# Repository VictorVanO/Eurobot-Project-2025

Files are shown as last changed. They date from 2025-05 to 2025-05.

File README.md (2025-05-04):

# Eurobot-Project-2025




# Table of contents

* [Project participants](#project-participants)
* [About the project](#question-about-the-project)
* [Getting started](#rocket-getting-started)
    * [Prerequesites](#exclamation-prerequesites)
* [Big Robot](#car-big-robot)
* [PAMI](#pami)
    * [Superstar](#star2-superstar)
    * [Groupie](#dancer-groupie)
* [Tree structure](#deciduous_tree-tree-structure)

# Project participants
- 20253 Van Olffen Victor
- 195030 Jardinet Louis
- 18194 Dufour Arthur
- 195105 Simpalingabo Ange
- 195357 Comor Edin
- 195052 Sahib Oussama

# :question: About the project
The purpose of this project is to participate in the [Eurobot Contest][eurobot] organised in 2025. The rules are available [here][eurobot-rules].

Our participation to this competition was necessary in order to validate the **Embedded Project** course given in 1st year of informatics/electronics at ECAM.

# :rocket: Getting started

This repository is a presentation of our robots and our strategies.

Anyone willing to replicate our robots should be able to do so using this repository.

Every file we used for our robots are listed here, aswell as the components and the schematics.

 Below is a photo of our robots (1 Big robot and 2 PAMI units):
 <p align="center">
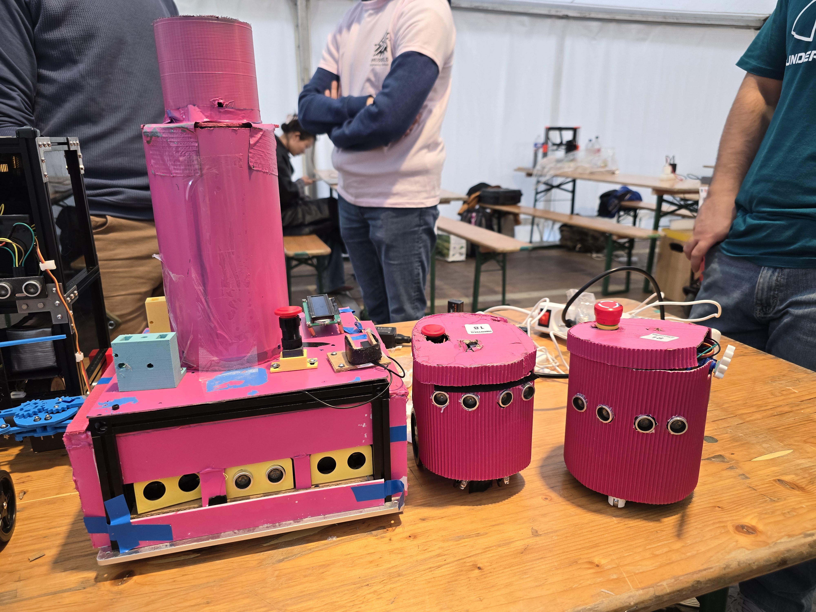
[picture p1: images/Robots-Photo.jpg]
Photo Robots
    
 </p>

## :exclamation: Prerequesites

To use our codes, you will need:
- [Arduino IDE][arduino] - To compile, debug and upload the .ino files into the arduino hardwares

You will also need to install these arduino libraries:
- LiquidCrystal_I2C
- Servo

# :car: Big Robot

## 🧩 Bloc Diagram
The Bloc diagram below shows the main components of the Big robot and how they are connected together.
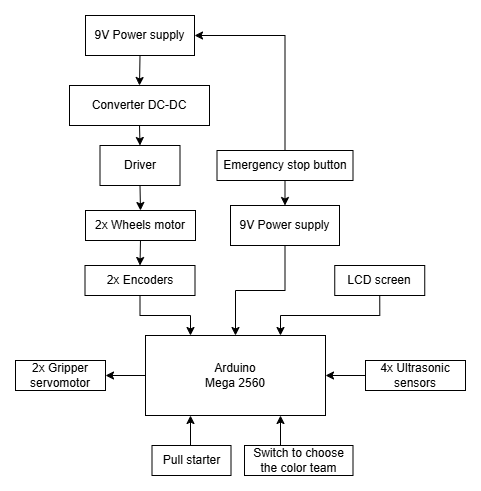
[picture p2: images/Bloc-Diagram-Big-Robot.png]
Bloc Diagram of the big robot.


## :memo: FSM

Our [initial FSM][fsm-big-robot-init] was ambitious, but due to a lack of time and components, our final FSM ended up like this:

Finite-State Machine of the big robot.

## :wrench: Components
Here are the main components for our robot : 
- 2 x 9V rechargeable power supplies to separately supply the driver and the microcontroller
- 2 x Voltage regulators
- 1 x Cytron MDD10A Dual Motors Driver
- 1 x Arduino Mega 2560
- 8 x HC-SR04 Ultrasonic sensors
- 2 x 3D Printed Robotic Arms
- 1 x Aluminium 25x25 cm frale
- 2 x DC Motors with corresponding wheels
- 1 x breadboard
- 1 x Emergency Button
- 1 x Starting Magnetic Reed
   
## Strategy
The Big Robot is designed to perform a specific sequence of actions to score points during the match:

1. **Banner Deployment :**  
   The robot starts by deploying the banner. The first gripper releases its tube, allowing the first banner holder to drop and clip into the edge of the table. Then, the robot moves forward by about 20 cm, and the second gripper releases the second tube, completing the deployment of the banner.

2. **Repositioning :**  
   After the banner is fully deployed, the robot reverses and begins its path toward the arrival zone, stopping right in front of it.

3. **Timed Entry :**  
   The robot waits until approximately the 85th second, allowing the 2 PAMI robots to clear the area.

4. **Final Movement :**  
   As soon as the area is clear, the Big Robot enters the arrival zone to secure end-of-match points.

## Schematic wiring

This is the schematic circuit of the big robot :
 
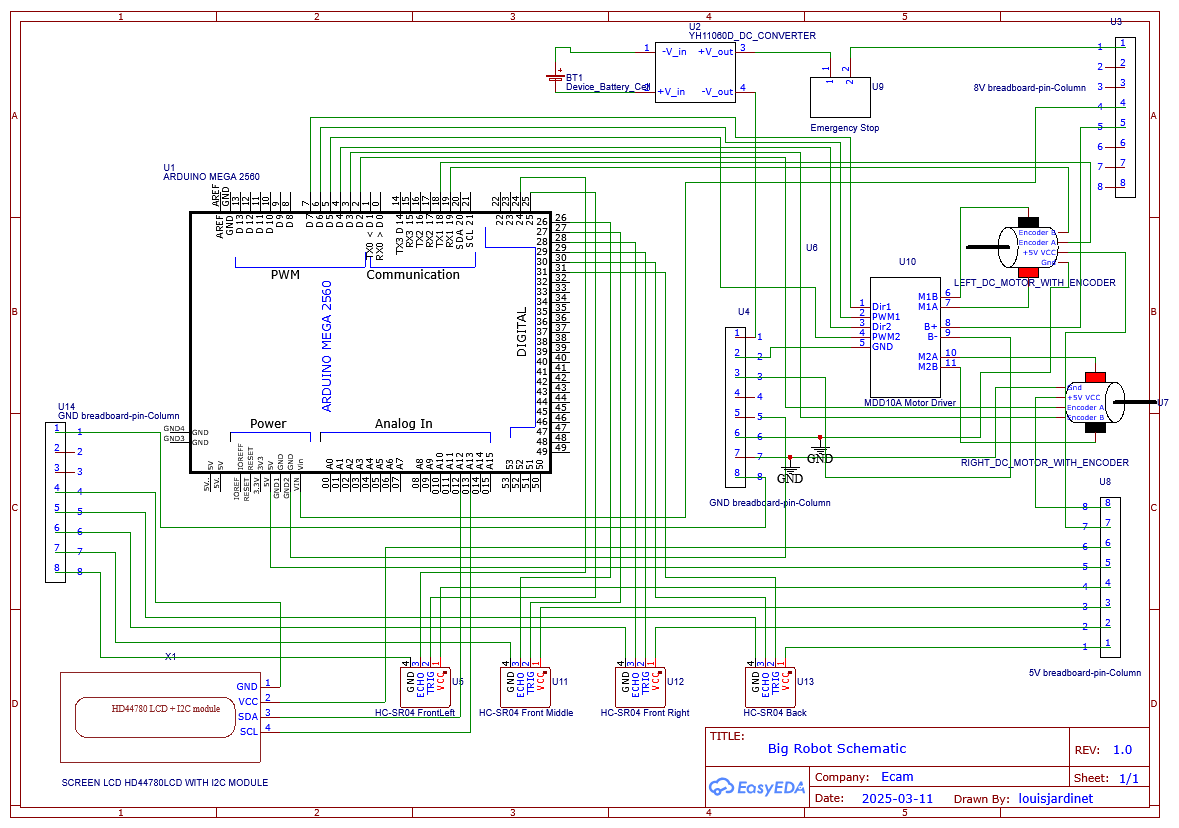
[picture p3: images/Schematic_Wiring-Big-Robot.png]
Schematic wiring of the big robot


## Grippers
The Big Robot is now equipped with 2 independent grippers, each controlled by a servo motor and mounted on a dedicated gripper support.
Each gripper holds one end of a tube, and each tube is attached to a banner holder shaped to fit the edge of the match table.
The banner itself measures 60 cm in length and 25 cm in height.

<p align="center">
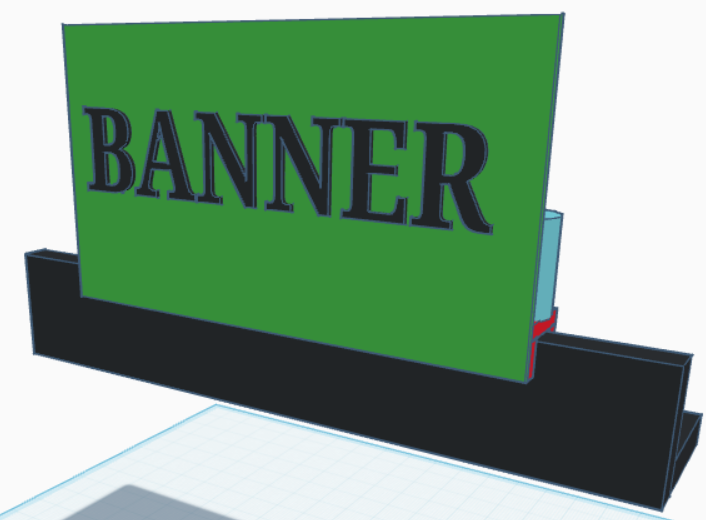
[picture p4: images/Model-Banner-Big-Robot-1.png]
Model Banner Step 1
  
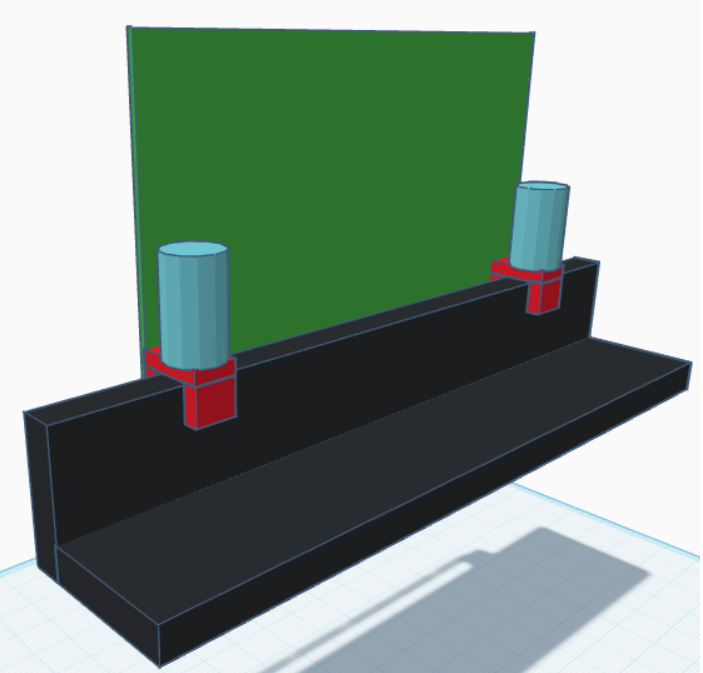
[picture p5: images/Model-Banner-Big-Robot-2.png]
Model Banner Step 2
  
</p>

During deployment, the robot releases the 1st tube, allowing the 1st banner holder to drop and clip into the table edge.
Then, the robot moves forward about 20 cm and releases the 2nd tube, completing the deployment of the banner.

In the ```3D-Models/big-robot``` folder, you’ll find the STL file for the gripper support. This part needs to be printed twice — once for each gripper:

| STL File | Required Quantity |
|---|---|
| gripper-support.stl | 2 |

# PAMI

## Components
 Here are the main components for ours PAMI's : 
 - 1 x Arduino Adafruits
 - 2 x HC-SR04 Ultrasonic sensors
 - 2 x Infrared sensors
 - 2 x DC Motors with corresponding wheels
 - 1 x breadboard
 - 1 x Emergency Button
 - 2 x Optical encoders
 - 1 x Servomotor
 - 1 x LED

# :star2: Superstar

## 🧩 Bloc Diagram
The Bloc diagram below shows the main components of the Superstar and how they are connected together :
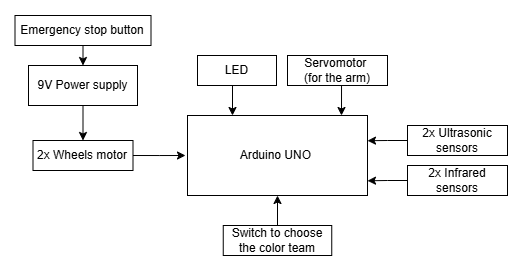
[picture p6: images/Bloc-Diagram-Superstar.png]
Bloc Diagram of the big robot.


## :memo: FSM

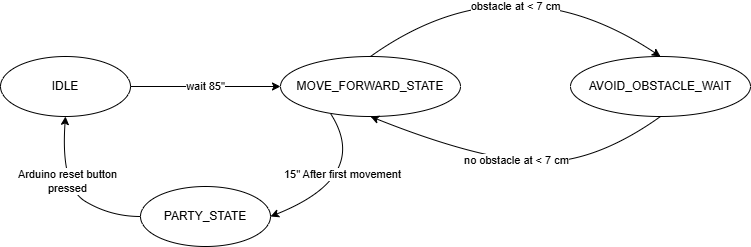
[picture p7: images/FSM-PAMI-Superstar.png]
Finite-State Machine of the PAMI superstar.


## Sensors

- **Distance Sensor (Ultrasonic)**  
    Detects obstacles from a distance to enable automatic avoidance and spatial orientation.

## Strategy
In order to score points the Superstar should be able to : 
1. The robot climbs the ramp by moving straight for 6 seconds at full speed.
2. It then turns right for 1.5 seconds to align itself as close as possible to the edge of the platform to maximize scoring potential.
3. It drives forward briefly to stabilize or adjust its final position.
4. Enter PARTY_STATE to celebrate the arrival. In this state, the robot rotates its servo motor arms back and forth and blinks the LED lights to provide a visual and animated signal.
   
## Obstacle Avoidance
When an obstacle is detected by the distance sensor, the robot stop until there is no more obstacle. 

## Schematic wiring

This is the schematic circuit of the superstar :

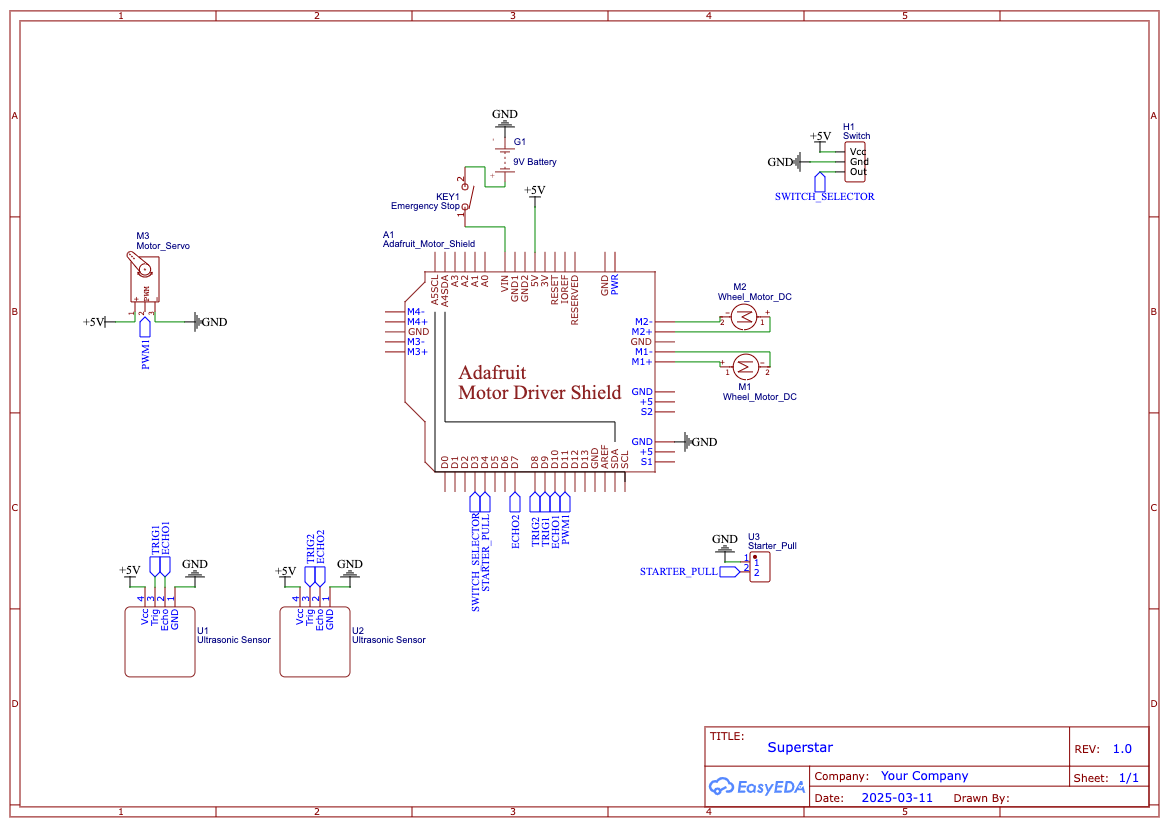
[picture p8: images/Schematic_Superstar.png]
Schematic wiring of the Superstar robot


### Obstacle Avoidance
When an obstacle is detected by the distance sensor, the robot stop until there is no more obstacle. 

## Assembly 
- The two motors and encoders are already placed on the chassis
- Glue the breadboard to the chassis
- With four M3x20mm screws, attach the Arduino mount on the second plate and place the Arduino in it
- With four M3x15mm standoff screws, assemble the two plates
- With two M3x30mm screws fix the Ultrasonic sensor mount on the front of the Arduino mount and slide the sensors into the support
- With two M3x20mm standoff screws fix the Servo/Emergency button mount on the rear of the Arduino mount and slide motor and the button into the support
- With two M3 screws and nuts fix the battery support to the lower plate

# :dancer: Groupie

## 🧩 Bloc Diagram
The Bloc diagram below shows the main components of the Groupie and how they are connected together :
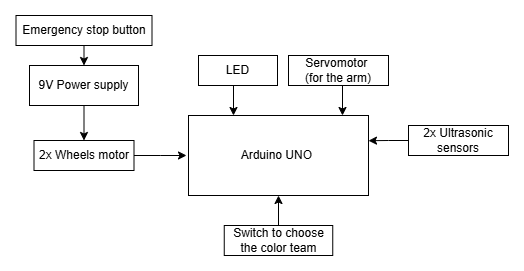
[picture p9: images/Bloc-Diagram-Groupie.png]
Bloc Diagram of the big robot.


## :memo: FSM

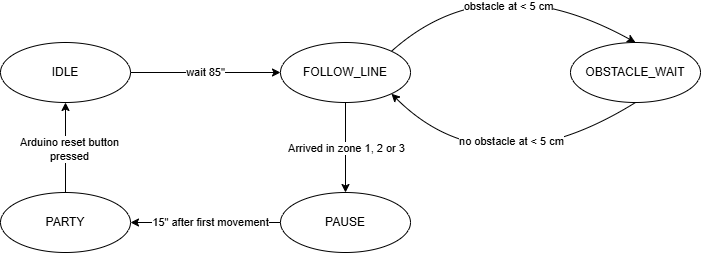
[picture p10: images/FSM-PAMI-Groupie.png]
Finite-State Machine of the PAMI groupie.


## Sensors

- **Infrared (IR) Sensors**  
    Used for line-following and distinguishing between black and white surfaces. Placed at the front of the robot, they allow it to follow a line on the ground or detect nearby obstacles.

- **Optical Fork Sensors (Encoders)**  
    Each wheel is equipped with a slotted disk attached to the motor shaft and an optical fork sensor that detects interruptions of the infrared beam caused by the slots. For every detected interruption, a pulse is generated on a microcontroller's digital input. This allows the robot to repeat the same movements on both wheels, improving synchronization and control.

- **Distance Sensor (Ultrasonic)**  
    Detects obstacles from a distance to enable automatic avoidance and spatial orientation.

## Strategy
In order to score points the groupie should be able to : 
1. Follow a line to reach the arrival zone. The robot follows a black line on a light surface using IR sensors. By analyzing the left/right sensor signals, it adjusts its trajectory to stay centered on the line.
2. Enter PARTY_STATE to celebrate the arrival. In this state, the robot rotates its servo motor arms back and forth and blinks the LED lights to provide a visual and animated signal.

## Schematic wiring

This is the schematic circuit of the groupie :

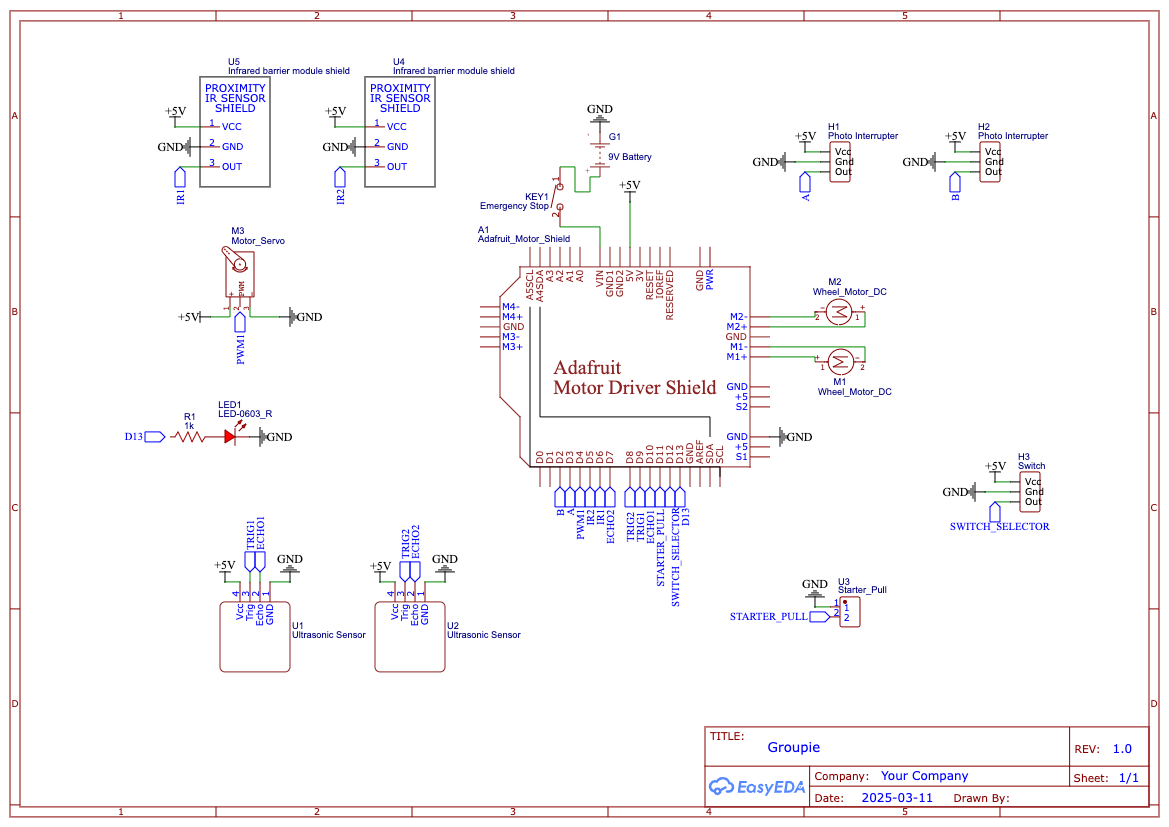
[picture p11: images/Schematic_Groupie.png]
Schematic wiring of the Groupie robot


## Obstacle Avoidance

When an obstacle is detected by the distance sensor, the robot interrupts line following and performs an avoidance maneuver based on a simple algorithm (stop, turn, go forwoard, turn).

## Assembly 
- Place the two motors on the first robot plate and assure that it is positioned on the appropriate holes. Mount the encoder wheels on the inside of the motors
- On the second plate, place the encoders on there dedicated mount 
- With two M3x15mm screws and nuts, fix the Infrared sensors mount at the front of the second plate and fix the sensors on the mount with two M3x15mm screws and nuts
- With four M3x20mm screws, attach the Arduino mount on the second plate and place the Arduino in it
- With four M3x15mm standoff screws, assemble the two red plates. Be sure to keep the motors well in place as they will fixed between the two plates and guide the encoder wheels trough the sensors
- With two M3x30mm screws fix the Ultrasonic sensor mount on the front of the Arduino mount and slide the sensors into the support
- With two M3x20mm standoff screws fix the Servo/Emergency button mount on the rear of the Arduino mount and slide motor and the button into the support

# :deciduous_tree: Tree Structure

```bash
Eurobot-Project-2025
    ├── 3D-models
       ├── big-robot
       ├── groupie-robot
       └── superstar-robot
    ├── big-robot
    ├── groupie-robot
    ├── images
    ├── superstar-robot
    ├── .gitignore
    ├── LICENSE
    └── README.md
```

<!-- Links -->
[eurobot]: https://www.eurobot.org/
[eurobot-rules]: https://www.eurobot.org/eurobot-contest/eurobot-2025/
[arduino]: https://www.arduino.cc/en/software/
[fsm-big-robot-init]: https://github.com/VictorVanO/Eurobot-Project-2025/blob/main/images/FSM-Big-Robot-init.png

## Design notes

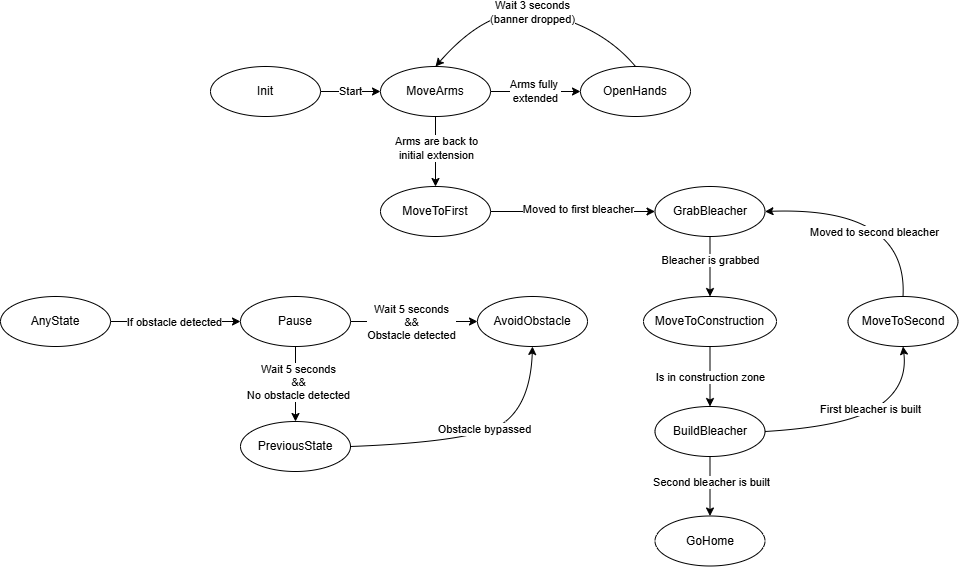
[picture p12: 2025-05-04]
images/FSM-Big-Robot-init.png

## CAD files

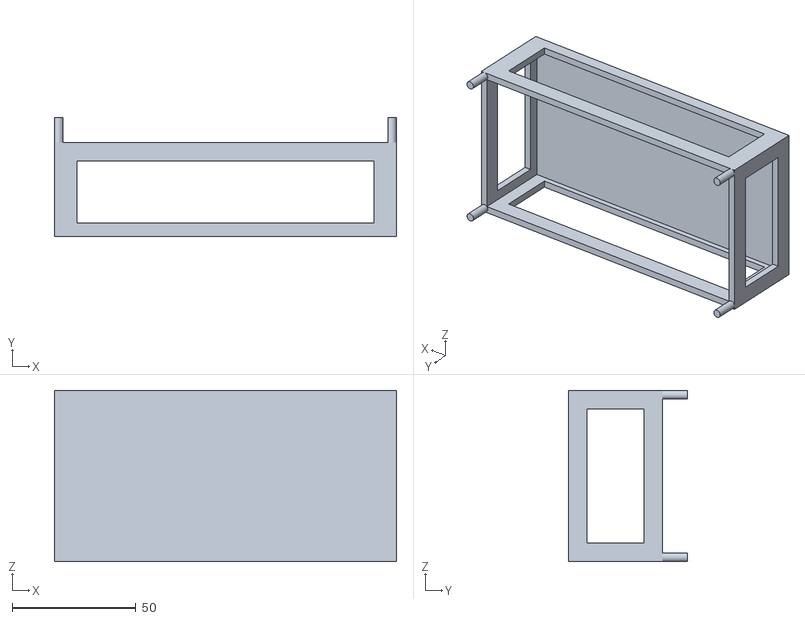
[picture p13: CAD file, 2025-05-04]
3D-models/big-robot/battery-regulator-support.stl
138.0 x 48.0 x 69.0

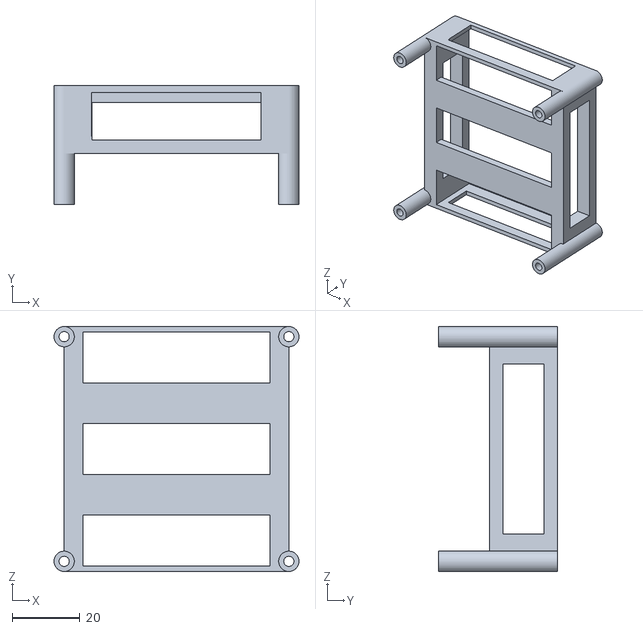
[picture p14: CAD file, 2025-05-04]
3D-models/groupie-robot/arduino-uno-support.stl
72.2 x 35.0 x 72.2

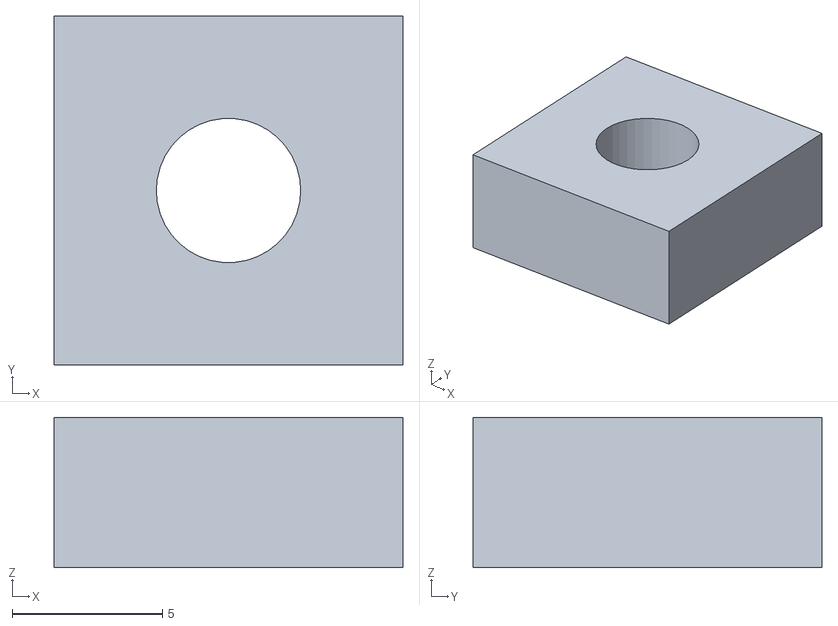
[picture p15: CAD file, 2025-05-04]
3D-models/groupie-robot/arm/arm-fix.stl
11.6 x 11.6 x 5.00

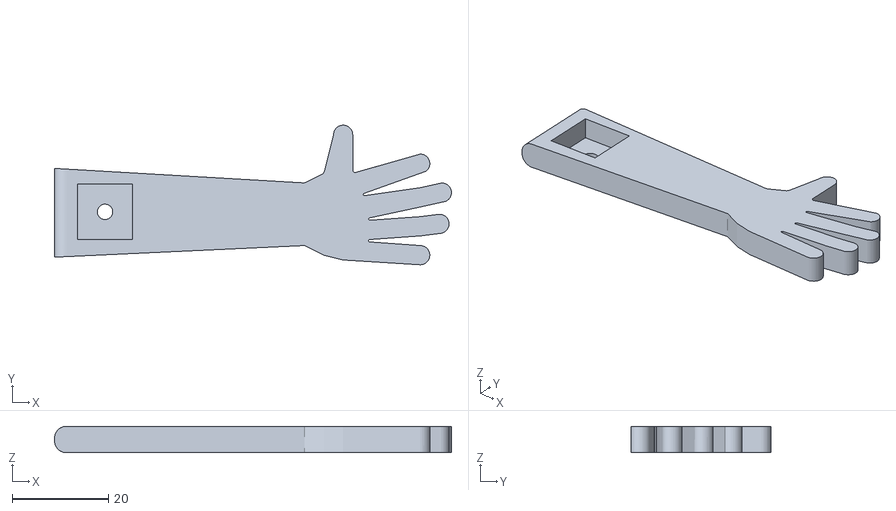
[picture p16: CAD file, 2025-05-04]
3D-models/superstar-robot/arm/arm.stl
82.4 x 29.0 x 5.50

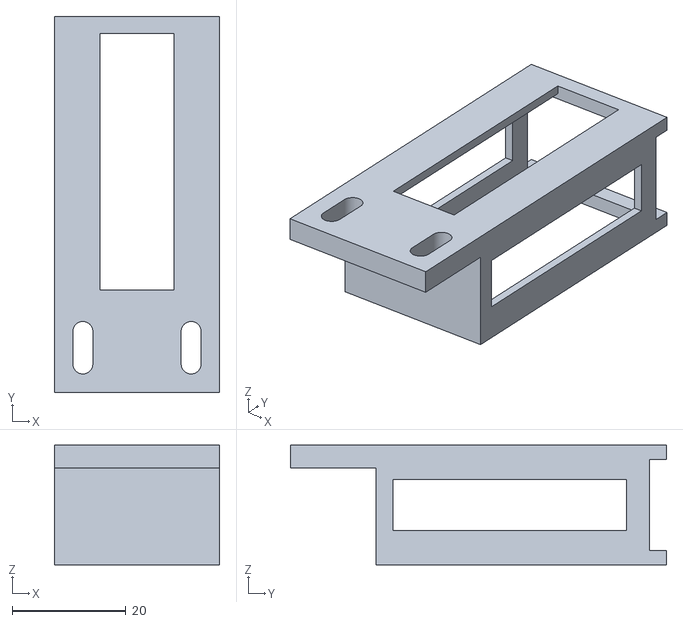
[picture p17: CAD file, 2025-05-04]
3D-models/superstar-robot/battery-support.stl
29.0 x 66.0 x 21.0

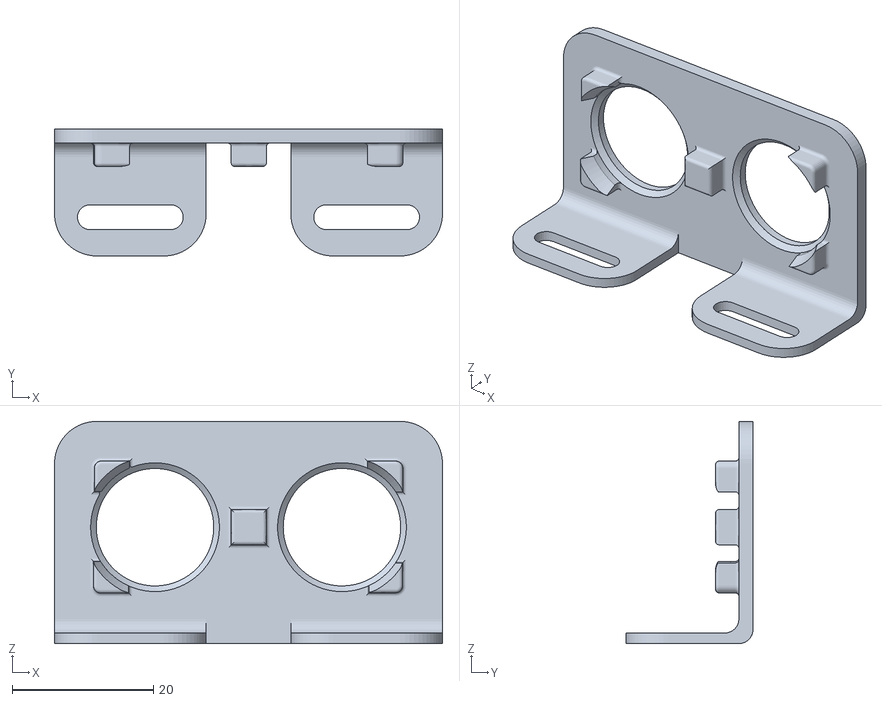
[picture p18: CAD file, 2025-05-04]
3D-models/big-robot/ultrasonic-sensor-support.stl
55.0 x 18.0 x 31.5

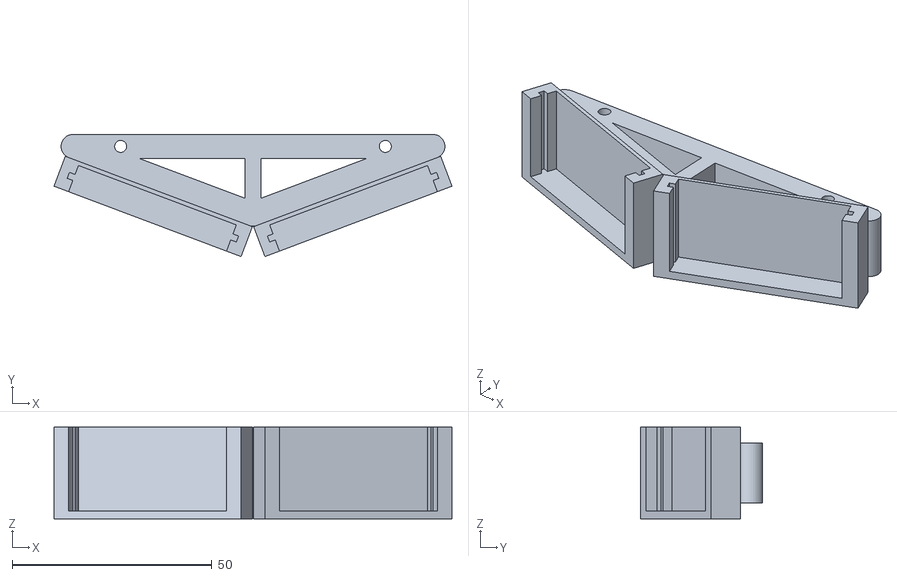
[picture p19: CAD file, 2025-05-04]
3D-models/groupie-robot/double-ultrasonic-sensor-support.stl
99.5 x 30.6 x 23.0

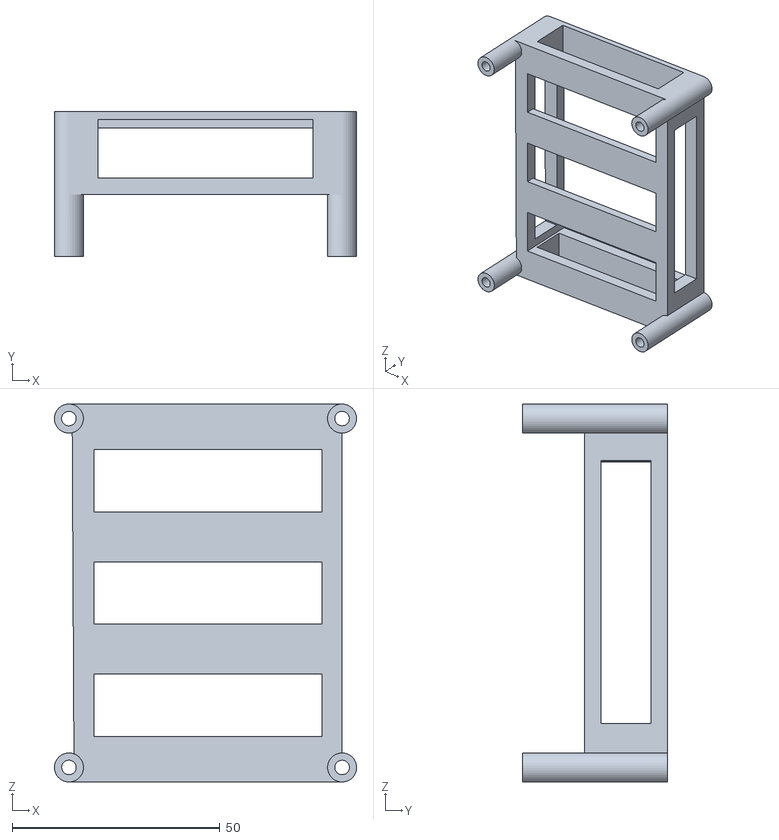
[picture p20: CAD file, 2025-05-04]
3D-models/superstar-robot/arduino-uno-support.stl
72.8 x 35.0 x 91.0

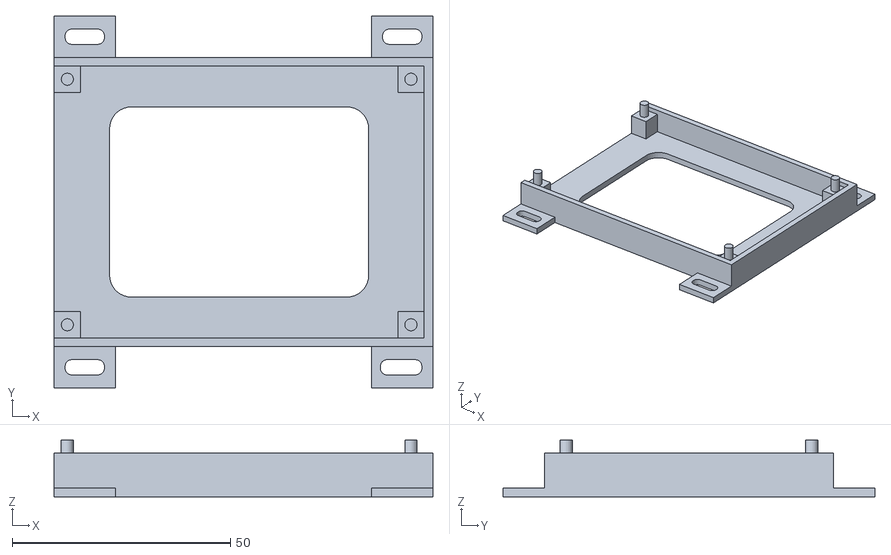
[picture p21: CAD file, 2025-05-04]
3D-models/big-robot/driver-motor-dc-support.stl
86.8 x 85.3 x 13.0

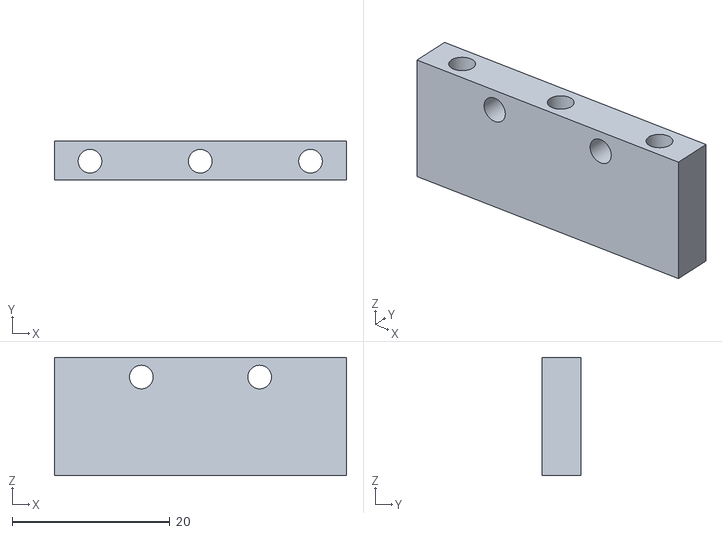
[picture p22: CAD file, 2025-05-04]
3D-models/groupie-robot/double-infrared-sensor-support.stl
37.0 x 5.00 x 15.0

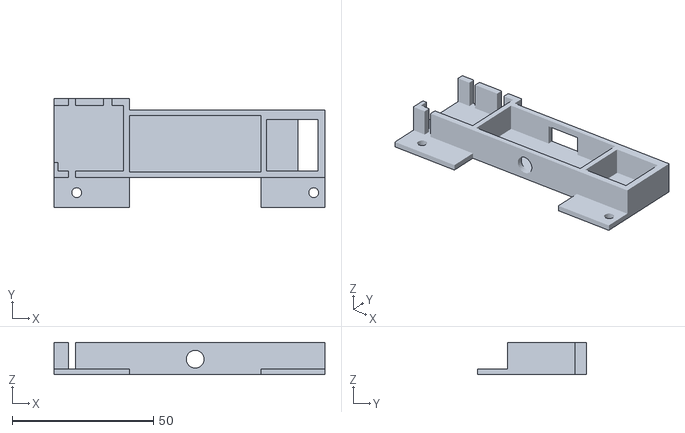
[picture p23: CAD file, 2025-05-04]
3D-models/superstar-robot/color-team-switch-emergency-stop-button-servomotor-support.stl
96.0 x 38.7 x 11.5

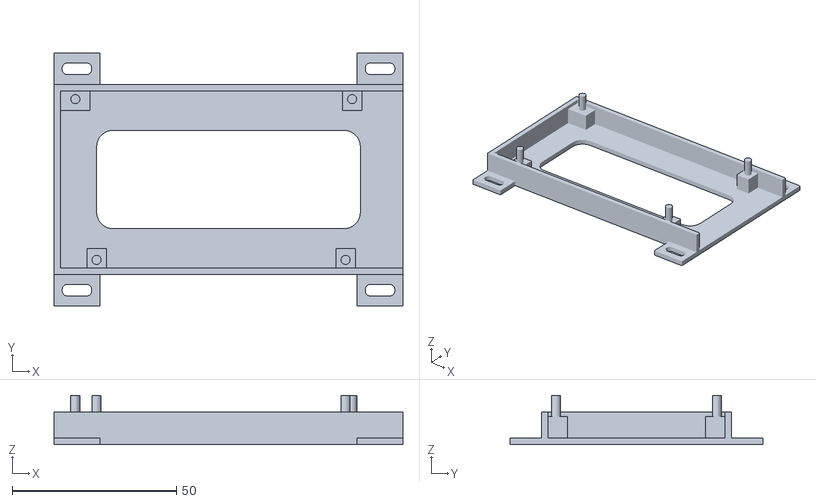
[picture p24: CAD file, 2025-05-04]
3D-models/big-robot/arduino-mega2560-support.stl
106.4 x 77.0 x 15.0

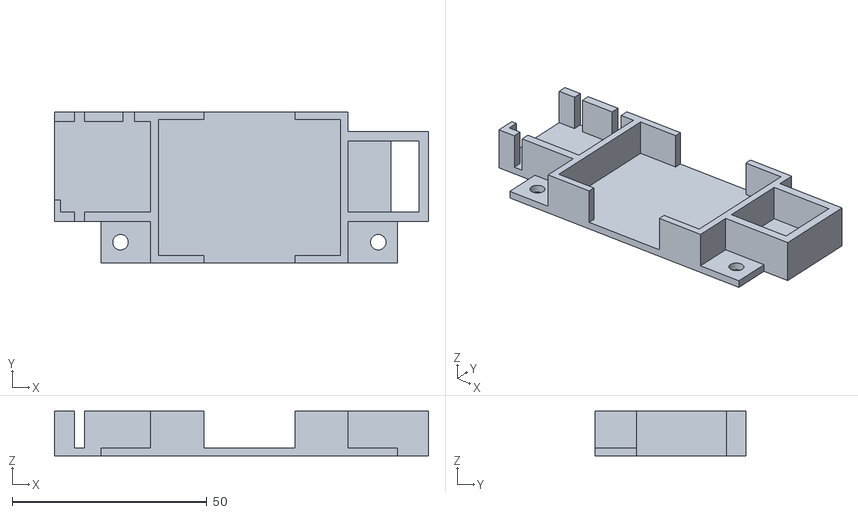
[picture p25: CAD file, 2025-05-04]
3D-models/groupie-robot/breadboard-emergency-stop-button-servomotor-support.stl
96.0 x 38.8 x 11.5

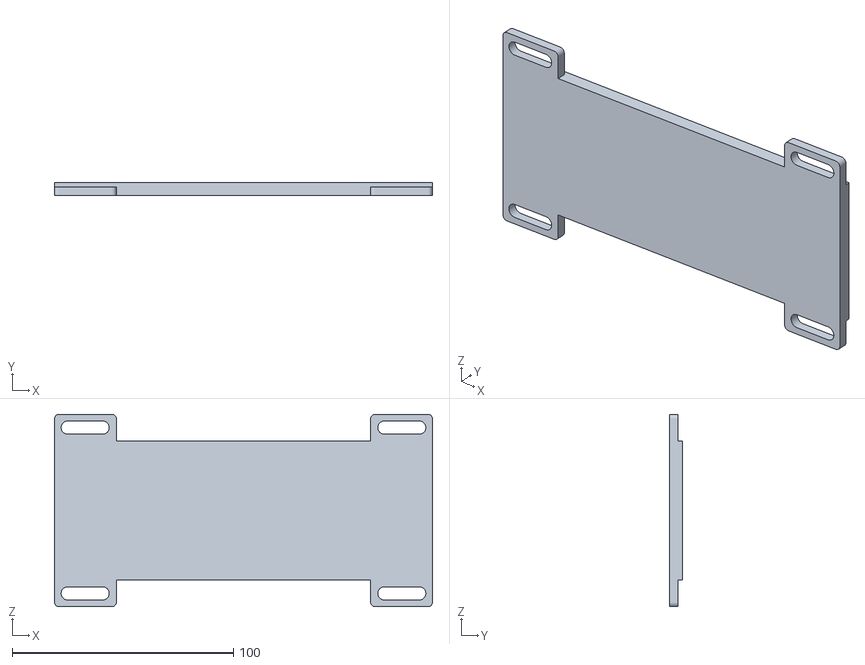
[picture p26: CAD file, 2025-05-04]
3D-models/big-robot/breadboard-support.stl
171.0 x 6.00 x 87.0

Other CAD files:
3D-models/superstar-robot/double-ultrasonic-sensor-support.stl
3D-models/big-robot/color-team-switch-support.stl
3D-models/big-robot/dc-regulator-support.stl
3D-models/big-robot/emergency-stop-button-support.stl
3D-models/big-robot/gripper-support.stl

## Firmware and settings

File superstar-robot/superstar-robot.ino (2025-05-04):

#include "FSM_Yellow.h"
#include "FSM_Blue.h"

const int modeSwitchPin = 3;
ModeSelector selector(modeSwitchPin);

const int pullPin = 4;
PullPin pullTrigger(pullPin);  

FSM_Yellow fsmYellow;
FSM_Blue fsmBlue;

bool startAuthorized = false;
bool useBlue = false;

void setup() {
    Serial.begin(9600);

    selector.begin();
    pullTrigger.begin();

    if (selector.isPrimaryMode()) {
        Serial.println("FSM_Blue selected");
        useBlue = true;
        fsmBlue.init();
    } else {
        Serial.println("FSM_Yellow selected");
        useBlue = false;
        fsmYellow.init();
    }
}

void loop() {
    // Wait for pull-pin to be removed before starting
    if (!startAuthorized) {
        if (!pullTrigger.isActivated()) {  // Logic stays the same (LOW = not pulled)
            startAuthorized = true;

            if (useBlue) {
                fsmBlue.authorizeStart();
            } else {
                fsmYellow.authorizeStart();
            }

        } else {
            delay(200);
            return;
        }
    }

    // Run the appropriate FSM
    if (useBlue) {
        fsmBlue.run();
    } else {
        fsmYellow.run();
    }

    delay(100);
}

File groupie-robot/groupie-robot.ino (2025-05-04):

#include "FSM_Yellow.h"   // Finite State Machine for the yellow configuration
#include "FSM_Blue.h"     // Finite State Machine for the blue configuration

// Pin used to determine the robot's mode (yellow or blue)
const int modeSwitchPin = 12;
ModeSelector selector(modeSwitchPin);

// Pin connected to the physical pull trigger (formerly "tirette")
const int pullPin = 11;
PullPin pullTrigger(pullPin);  // Manages start signal

// FSM instances
FSM_Yellow fsmYellow;
FSM_Blue fsmBlue;

// Flags to track system state
bool startAuthorized = false;  // Indicates if the robot is allowed to start
bool useBlue = false;          // Determines whether to run the blue FSM or the yellow FSM

void setup() {
    Serial.begin(9600);

    // Initialize selector and pull trigger hardware
    selector.begin();
    pullTrigger.begin();

    // Determine mode based on the selector state
    if (selector.isPrimaryMode()) {
        Serial.println("FSM_Blue selected");
        useBlue = true;
        fsmBlue.init();  // Initialize the blue FSM
    } else {
        Serial.println("FSM_Yellow selected");
        useBlue = false;
        fsmYellow.init();  // Initialize the yellow FSM
    }
}

void loop() {
    // Wait for the pull trigger to be activated before starting
    if (!startAuthorized) {
        if (pullTrigger.isActivated()) {
            startAuthorized = true;

            // Notify the selected FSM to begin
            if (useBlue) {
                fsmBlue.authorizeStart();
            } else {
                fsmYellow.authorizeStart();
            }
        } else {
            // Wait and check again later
            delay(200);
            return;
        }
    }

    // Run the appropriate FSM
    if (useBlue) {
        fsmBlue.run();
    } else {
        fsmYellow.run();
    }

    // Small delay to avoid overloading the loop
    delay(100);
}

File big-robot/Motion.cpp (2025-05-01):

#include <Arduino.h>
#include "Motors.h"
#include "Encoders.h"
#include "Motion.h"

// State tracking
static unsigned long prevT = 0;
static float eprevR = 0, eprevL = 0;
static float eintegralR = 0, eintegralL = 0;
static long targetLeft = 0, targetRight = 0;
static bool motionActive = false;
static MotionType currentMotion = MOTION_NONE;

static int pmax = 235;
static int pmin = 25;

static int neutralZone = 15;
static int neutralTimeout = 200;

static bool leftDone = false, rightDone = false;
static unsigned long neutralStartL = 0, neutralStartR = 0;

// For GO_HOME recovery
static float resumeTargetLeft = 0;
static float resumeTargetRight = 0;
static bool resumeRightWheelOnly = false;
static bool resumeSmoothRotate = false;

void startGoStraight(float distance_cm) {
    resetEncoders();
    resetPIDVariables();
    currentMotion = MOTION_STRAIGHT;
    targetLeft = distance_cm * 80.0;
    targetRight = distance_cm * 80.0;
    resumeTargetLeft = targetLeft;
    resumeTargetRight = targetRight;
    resumeSmoothRotate = false;
    motionActive = true;
}

void startRotate(long angle_deg) {
    resetEncoders();
    resetPIDVariables();
    currentMotion = MOTION_ROTATE;
    float ticks = angle_deg * 14.75;
    targetLeft = ticks;
    targetRight = -ticks;
    resumeTargetLeft = targetLeft;
    resumeTargetRight = targetRight;
    resumeSmoothRotate = false;
    motionActive = true;
}

void startSmoothRotate(long angle_deg, bool rightWheel) {
    resetEncoders();
    resetPIDVariables();
    currentMotion = MOTION_SMOOTH_ROTATE;
    float ticks = abs(angle_deg) * 29.5;
    if (rightWheel) {
        targetLeft = 0;
        targetRight = (angle_deg > 0 ? ticks : -ticks);
    } else {
        targetLeft = (angle_deg > 0 ? ticks : -ticks);
        targetRight = 0;
    }
    resumeTargetLeft = targetLeft;
    resumeTargetRight = targetRight;
    resumeRightWheelOnly = rightWheel;
    resumeSmoothRotate = true;
    motionActive = true;
}

void resumeMotion() {
    motionActive = true;
    if (resumeSmoothRotate) {
        currentMotion = MOTION_SMOOTH_ROTATE;
    } else if (resumeTargetLeft == resumeTargetRight) {
        currentMotion = MOTION_STRAIGHT;
    } else {
        currentMotion = MOTION_ROTATE;
    }
}

void updateMotion() {
    if (!motionActive) return;

    long currT = micros();
    float deltaT = (currT - prevT) / 1e6;
    prevT = currT;

    long posL = getEncoderLeft();
    long posR = getEncoderRight();

    long errL = targetLeft - posL;
    long errR = targetRight - posR;

    float dedtL = (errL - eprevL) / deltaT;
    float dedtR = (errR - eprevR) / deltaT;

    eintegralL += errL * deltaT;
    eintegralR += errR * deltaT;

    eintegralL = constrain(eintegralL, -300, 300);
    eintegralR = constrain(eintegralR, -300, 300);

    float kp = 1.0, ki = 0.07, kd = 0.0;

    float uL = kp * errL + ki * eintegralL + kd * dedtL;
    float uR = kp * errR + ki * eintegralR + kd * dedtR;

    int pwrL = constrain((int)fabs(uL), pmin, pmax);
    int pwrR = constrain((int)fabs(uR), pmin, pmax);

    int dirL = errL > 0 ? 1 : 0;
    int dirR = errR > 0 ? 1 : 0;

    // Neutral zone logic
    if (abs(errL) < neutralZone) {
        if (!leftDone) {
            if (neutralStartL == 0) neutralStartL = millis();
            if (millis() - neutralStartL > neutralTimeout) {
                pwrL = 0;
                dirL = 0;
                leftDone = true;
            }
        }
    } else {
        neutralStartL = 0;
        leftDone = false;
    }

    if (abs(errR) < neutralZone) {
        if (!rightDone) {
            if (neutralStartR == 0) neutralStartR = millis();
            if (millis() - neutralStartR > neutralTimeout) {
                pwrR = 0;
                dirR = 0;
                rightDone = true;
            }
        }
    } else {
        neutralStartR = 0;
        rightDone = false;
    }

    setMotor(dirL, pwrL, PWM_1, DIR_1);
    setMotor(dirR, pwrR, PWM_2, DIR_2);

    eprevL = errL;
    eprevR = errR;

    if (leftDone && rightDone) {
        stopMotors();
        motionActive = false;
        currentMotion = MOTION_NONE;
    }
}

void resetPIDVariables() {
    prevT = micros();
    eprevL = eprevR = 0;
    eintegralL = eintegralR = 0;
    leftDone = rightDone = false;
    neutralStartL = neutralStartR = 0;
}

bool isMotionComplete() {
    return !motionActive;
}

MotionType getCurrentMotionType() {
    return currentMotion;
}

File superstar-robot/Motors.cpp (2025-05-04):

#include "Motors.h"

Adafruit_MotorShield AFMS = Adafruit_MotorShield();
Adafruit_DCMotor *motor1 = AFMS.getMotor(1);
Adafruit_DCMotor *motor2 = AFMS.getMotor(2);

void initMotors() {
  AFMS.begin();
}

void setMotorsSpeed(uint8_t speed) {
  motor1->setSpeed(speed);
  motor2->setSpeed(speed - 10);
}

void runMotors(uint8_t direction) {
  motor1->run(direction);
  motor2->run(direction);
}

void turnLeft() {
    motor1->run(RELEASE);
    motor2->run(FORWARD);
}

void goForward(){
    motor1->run(FORWARD);
    motor2->run(FORWARD);
}

void turnRight() {
    motor1->run(FORWARD);
    motor2->run(RELEASE);
}

void stopMotors() {  
    motor1->run(RELEASE);
    motor2->run(RELEASE);
}

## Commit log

2025-02-07 Added PAMI Groupie FSM and his sensors
2025-02-14 Added Big Robot initial FSM, motors and ultrasonic. PAMI Groupie renamed
2025-02-21 Updated big robot motors functions
2025-02-21 Added initialization of multiple ultrasonic sensors for the big robot
2025-02-21 Changed ultrasonic sensors pins
2025-02-21 Updated ultrasonic sensors initialization and updated FSM obstacle detection
2025-02-27 Added new ultrasonic handling versions
2025-02-27 Final ultrasonic sensors integration version
2025-02-27 Added new motors functions and implementation in FSM
2025-02-27 Fixed pin names init errors
    [FSM.cpp, Motors.cpp]
2025-02-28 Added LCD prints in every FSM state
2025-02-28 Added Avoid Obstacle state
    [FSM.cpp, Ultrasonic.h]
2025-03-11 Added STL files for big robot base
    [arduino mega 2560 support.stl, driver motor DC support.stl, emergency-stop button support.stl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]
2025-03-11 Added STL files for big robot arm
    [arm n°1.stl, arm n°2.stl]
2025-03-11 Added STL files for superstar and groupie
    [arm.stl, breadboard, emergency-stop button, servomotor support.stl]
2025-03-13 Correction of STL file names
    [arduino-mega2560-support.stl, arm-1.stl, arm-2.stl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]
2025-03-14 removed groupie-robot from the wrong branch
    [Bluetooth.cpp, Infrared.cpp, Motors.cpp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]
2025-03-14 Added servomotor arms configuration
2025-03-14 Added servomotors files
2025-03-14 updated fsm with arms movement and fixed issues
    [FSM.cpp]
2025-03-25 add a timer to end the seqeunce if it's possible even if there is an object for few sec
2025-03-26 New stl files for the groupie
    [arduino-uno-support.stl, arm-fix.stl, infrarouge-double-led.stl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]
2025-03-26 New stl files for the superstar
    [arduino-uno-support.stl, arm-fix.stl, pile-support.stl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]
2025-03-26 New stl files for the arm of the big robot
    [arm-base.stl, arm-hub.stl, bas-part-1.stl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]
2025-03-27 add motors + ultrasonic
2025-03-27 Read the Ultrasonic again before go out of the state await obstacle
2025-03-27 add implementation infrared sensor
2025-03-27 Adjust ultrasonic
2025-03-28 Add avoid obstacle sequence + Button to handlestate
2025-03-29 Change the pin of the button
2025-03-29 Add encoders sensors to the strategie
2025-03-29 Avoid obstacle then check before continue the sequence and if there is a other obstacle stop the robot
    [Motors.cpp]
2025-04-01 Update README.md
    Groupie mounting instructions updated
2025-04-01 Name error
    [base-part-1.stl]
2025-04-01 Rename of some STL files
    [base-bolt.stl, base-part-3.stl]
2025-04-01 Added STL file for the Team color switch
    [color-team-switch-support.stl]
2025-04-01 Correction of Superstar STL for switch-emergency stop-servomotor support
    [breadboard-emergency-stop-button-servomotor-support.stl, color-team-switch-emergency-stop-button-servomotor-support.stl]
2025-04-07 Added 3 ultrasonic sensors and remove unit tests file causing errors
    [FSM.cpp, Ultrasonic.h]
2025-04-07 Adjust the wheel speed with the new weight
2025-04-08 Changed servomotors pins
2025-04-08 Changed FSM AVOID_OBSTACLE state steps management
    [FSM.cpp]
2025-04-08 Integrate the switch selector for the color
2025-04-08 Changed avoid obstacle state steps and obstacle detection
    [FSM.cpp, Ultrasonic.h]
2025-04-08 Add the servo to the function "party"
2025-04-08 Fixed issues with front and back obstacle detection
    [FSM.cpp]
2025-04-11 Updated avoid obstacle movements and changed obstacle detection treshold
    [FSM.cpp]
2025-04-11 servo ok, led no ok
2025-04-15 PID implementation into the robot and updated FSM states with new strategy
2025-04-15 Changed ultrasonic sensors pins and removed servoarms from fsm
2025-04-18 adjust timer for the match + button
2025-04-18 Fixed obstacle detection with PID movements
    [FSM.cpp, Motion.cpp]
2025-04-18 Added Zipper and updated pid
2025-04-18 Finished Yellow zone movements & Added dynamic timers
2025-04-18 Fixed ulrasonic deactivation during yellow zone movements
    [FSM.cpp]
2025-04-18 Added new servomotors init
2025-04-19 change the compensation of the left encoder for avoid evitemment
2025-04-20 change the speed of the motor
2025-04-28 Added wiring schematic of the big Robot
2025-04-28 schematic wiring update
    Moved some labels in the big robot schematic wiring file
2025-04-28 Update README.md to add wiring schematic
2025-04-29 Removed unused avoid obstacle state
    [FSM.cpp]
2025-05-03 Update README.md
    Assembly sections added for the Pamis
2025-05-03 Update README.md for the grippers of the Big Robot
2025-05-04 Organized STL files for Big Robot and deleted obsolete arm files
    [arduino-mega2560-support.stl, arm-1.stl, arm-2.stl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]
2025-05-04 Added STL files for the support of the grippers for Big robot
    [gripper-support.stl]
2025-05-04 Removed STL file for Raspberry support
    [raspberry-support.stl]
2025-05-04 Added STL file for double infrared sensor support
    [double-infrared-sensor-support.stl]
2025-05-04 Renamed some STL files to English
    [battery-support.stl, double-ultrasonic-sensor-support.stl]
